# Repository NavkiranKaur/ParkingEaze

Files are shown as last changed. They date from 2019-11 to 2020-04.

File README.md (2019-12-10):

# ParkingEaze Project
## Build instructions
## Bipolar Stepper motor driven by Drv8825 driver on the raspberry pi broadcom platform
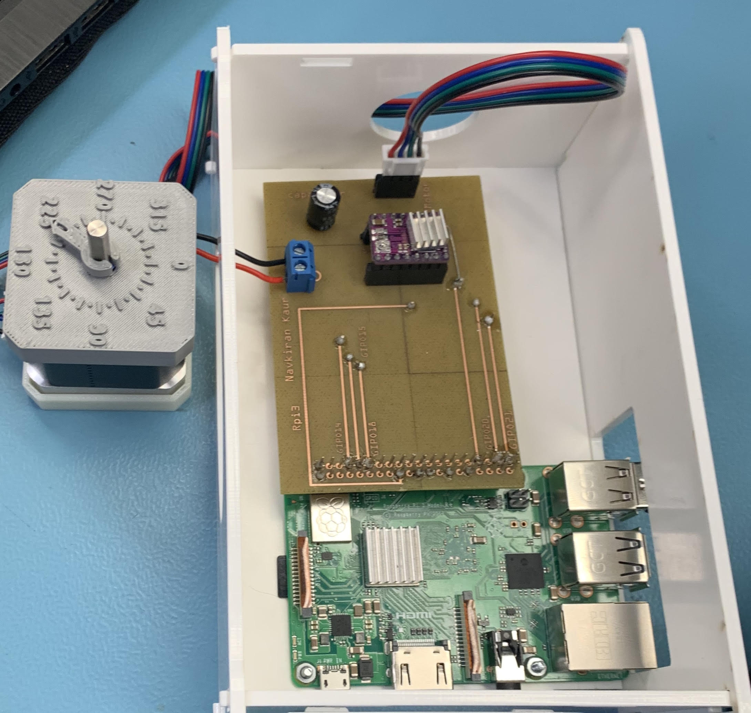
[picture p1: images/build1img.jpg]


## Purpose
The ParkingEaze Capstone Project : The stepper motor will be able to move the barriers in the car parking in order to allow the entrance and exit of the vehicle using the rotational movement controlled by the driver and raspberry pi Broadcom.
## Table of Contents
1. [Introduction](#introduction)
2. [System Diagram](#system-Diagram)
3. [Materials](#materials)
4. [Budget](#budget)
5. [Time Commitment](#time-Commitment)
6. [Setting up Raspberry Pi](#setting-Up-Raspberry-Pi)
7. [Mechanical Assembly](#mechanical-Assembly)
8. [PCB Soldering](#pcb-Soldering)
9. [PCB Power up](#pcb-power-up)
10. [Unit Testing](#unit-Testing)
11. [Enclosure](#enclosure)
12. [Production Testing](#production-Testing)

##  Introduction
In this project,bipolar stepper motor that is Nema 17 is driven by the DRV8825 driver on the raspberry pi development platform.Here are the build instructions that demonstrates how to control bi-polar stepper motors on a Raspberry Pi in Python using a DRV-8825 stepper motor driver.

## System Diagram 
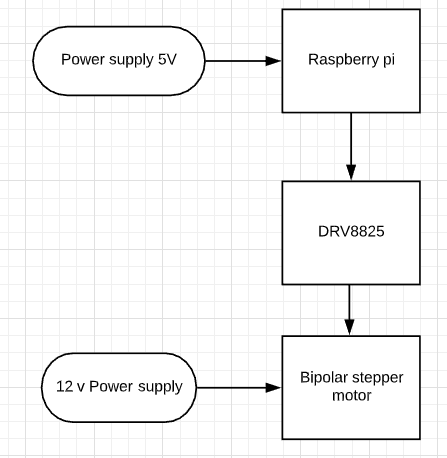
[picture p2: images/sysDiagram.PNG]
systemdiagram


## Materials
- Raspberry Pi 3B+ 
- [Hdmi cable](https://www.amazon.ca/gp/product/B07BN874RP/ref=ppx_yo_dt_b_asin_title_o02_s00?ie=UTF8&psc=1)
- [Bipolar steper motor Nema 17](https://www.amazon.ca/gp/product/B07C1MVTZC/ref=ppx_yo_dt_b_asin_title_o08_s00?ie=UTF8&psc=1)
- [Drv8825 driver](https://www.amazon.ca/gp/product/B07L2TKLPW/ref=ppx_yo_dt_b_asin_title_o08_s00?ie=UTF8&psc=1)
- [12 Voltage dc power supply portable adapt3r](https://www.amazon.ca/gp/product/B06X1BJRCS/ref=ppx_yo_dt_b_asin_title_o06_s00?ie=UTF8&psc=1)
- [Safety Glasses](https://www.amazon.ca/gp/product/B007YCMOCE/ref=ppx_yo_dt_b_asin_title_o05_s00?ie=UTF8&psc=1)
- power supply of the pi,mouse and keyboard
- 100 microFarad capacitor
- Breadboard and jumper wires (male and female)
- 40 pin male double row male to female header, 
- two 8 pins male to female headers and one 4 pin header ( all single row)
- Acrylic case for the enclosure 
- Get my Corel Draw file by clicking [here](https://github.com/NavkiranKaur/ParkingEaze/blob/master/mechanical/EnclosureFinal.cdr) for the enclosure
- 3d printed motor parts 
- Click [Here](https://github.com/NavkiranKaur/ParkingEaze/tree/master/mechanical/Nema%2017%20motor%203D%20printing%20files) to get my 3D printing files for the motor enclosure
-I suggest you to have them earlier so you could save your time instead of making them at the last end.

## Budget
- The main stuff and the materials required to build the project are listed below
The equipments that I have used from my parts kit are Jumper wires(both male and female),screw driver ,100 microFarad capacitor.I listed them here as in my budget my parts kit is mentioned,not the specific parts that I used.All the parts are bought from amazon except the parts that I already owned and the mouse,keyboard combo that is bought from Walmart.
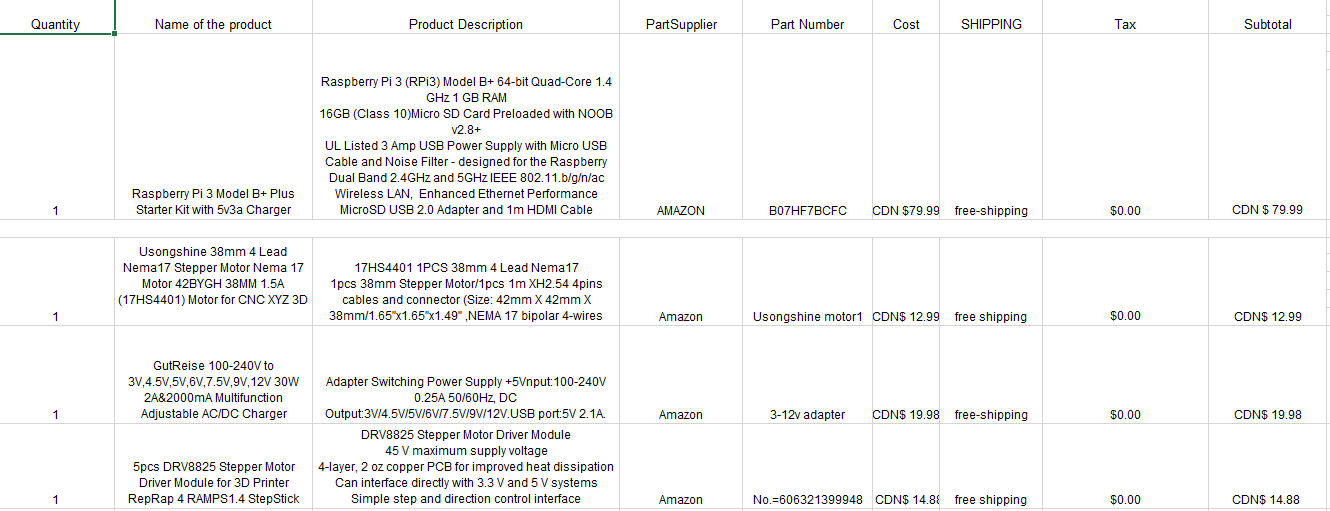
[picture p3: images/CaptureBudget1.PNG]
capture

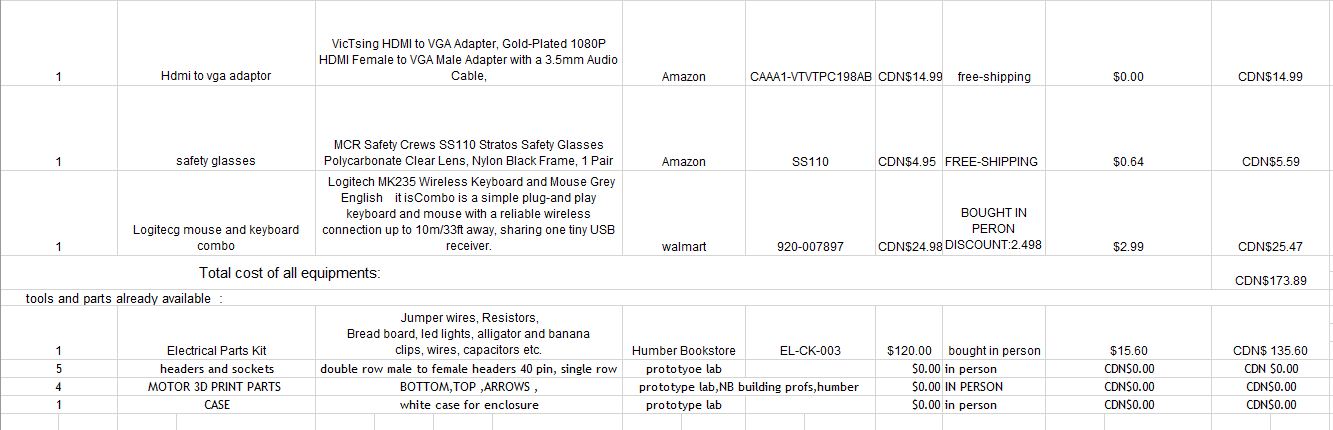
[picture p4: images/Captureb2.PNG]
capture


## Time commitment
- Overall project can be done in couple of days depends on the getting pcb made,alongwith making an enclosure for the equipments once they are built and connected.Also,depends upon the arrival of the materials for building hardware project.
In my case,I got delay in my breadboard due to not setting current voltage specifications on the driver,also made the pcb second time and also spent more time on the enclosure as it was 3D printing for the motor and my case was also big consisiting of pcb on the pi with the driver on it.So,if to be explained in more depth by knowing and being prepared what to do ,it can save much time.Breadboard can take 1 or 2 hours as to set all the voltages and making connections and based on that getting the pcb ready.Powering up take about 20 minutes and then getting the parts enclosed.

## Setting up raspberry pi
Connecting the raspberry with power supply,hdmi cable from raspberry pi to the hdmi to vga cable and that vga side to the monitor.Connecting the separate mouse and the keyboard with the pi.
Following the steps below:
1. Download [Raspbian](https://www.raspberrypi.org/downloads/) to be installed on your raspberry pi.
2. Use [SDCardFormatter](https://www.sdcard.org/downloads/formatter_4/) to format your SD card so for getting the pi to work
3. Inserting the SD card in raspberry pi and ensuring the connection all the above mentioned parts to be connected appropriately.
4. Switch on the power and finish the further setup including changing the settings.
5. Giving the commands on the terminal that require insallation like sudo updates etc,

## Mechanical Assembly
For the mechanical assembly,ensure connecting the pins and connections carefully.
Firstly the connections were made on the breadboard using the jumper wires from the driver ,raspberry pi ,stepper motor and the capacitor.I made the connections from driver to the raspberry pi ,motor and the capacitor and also used the power supply of the college. Breadboarding is just to make sure if the effectors and the components works as expected or their is a need to change some connections or if there is a damaged component.

## Wiring connections
-Raspberry pi pin 3v : DRV8825 SLEEP,DRV8825 RESET 
- Where connecting the sleep and reset together whereas connecting pi to the one of them
- Raspberry pi pin GND : DRV8825 GND1
- Raspberry pi pin GPIO21 : DRV8825 STEP
- Raspberry pi pin GPIO20 : DRV8825 DIRECTION
- Raspberry pi pin GPIO14 : DRV8825 MS1
- Raspberry pi pin GPIO15 : DRV8825 MS2
- Raspberry pi pin GPIO18 : DRV8825 MS3

ALSO IN DRV8825
-DRV8825 GROUND 1 TO BE CONNECTED WITH GROUND2 of DRV8825 itself
-In order to bind the motor wire pins with the drv8825
- Motor has two coil pairs Coil pair 1 ,coil pair 2
- Coil pair 1 includes A and C
- Coil pair 2 includes B and D
- MOTOR A WIRE PIN : DRV8825 OUT 2B
- MOTOR C WIRE  PIN: DRV8825 OUT 2A
- MOTOR B WIRE PIN : DRV8825  OUT 1A
- MOTOR D WIRE  PIN: DRV8825  OUT 1B

- MOTOR POWER SUPPLY ADAPTOR OF 12 V
- Capacitor (positive side) : DRV8825 VOLTAGE PIN : POWER SUPPLY POSITIVE (12V)
- Capacitor(negative side): DRV8825 GROUND: POWER SUPPLY GROUND

- Pin can be connected vice versa but make sure coil pair pins goes with the pair on the driver ,not interchanging if connecting a pair both pins to be connected to other driver pair itself. Don’t connect the pin in the pairs differently.

This [tutorial](https://www.rototron.info/raspberry-pi-stepper-motor-tutorial/) can also help you in depth with the required specifications.

--My breadboard design in the fritzing
capture
<!--![capture](https://raw.githubusercontent.com/NavkiranKaur/ParkingEaze/master/images/bread2.jpg)
![capture](https://raw.githubusercontent.com/NavkiranKaur/ParkingEaze/master/images/bread3.jpg) -->

- Also you need the code to run it,that i will be describing in the later steps below.

## PCB Soldering
Before starting the pcb soldering,make sure you watch this [video](youtube.com/watchv=BLfXXRfRIzY&list=PLQ32vZrF5U2lFOJTtZDytBWBYVLNp4RYz) and make sure to wear safety glasses.
The pcb is designed as followed by connections made and tested using the breadboard.
The pcb design is shown below designed in fritzing
capture
The pcb is made and then after it is soldered carefully
- Remember in my pcb design I put my drv8825 ground to ground connection on differnt side layer(yellow) than the soldering connecting pins (which are in orange).Make sure to keep it as same layer as other drv8825 connections.Hence ,you can see in my pcb ,i coonected an insulated red colour wire on same side where other drv8825 wires are connnected to pins.
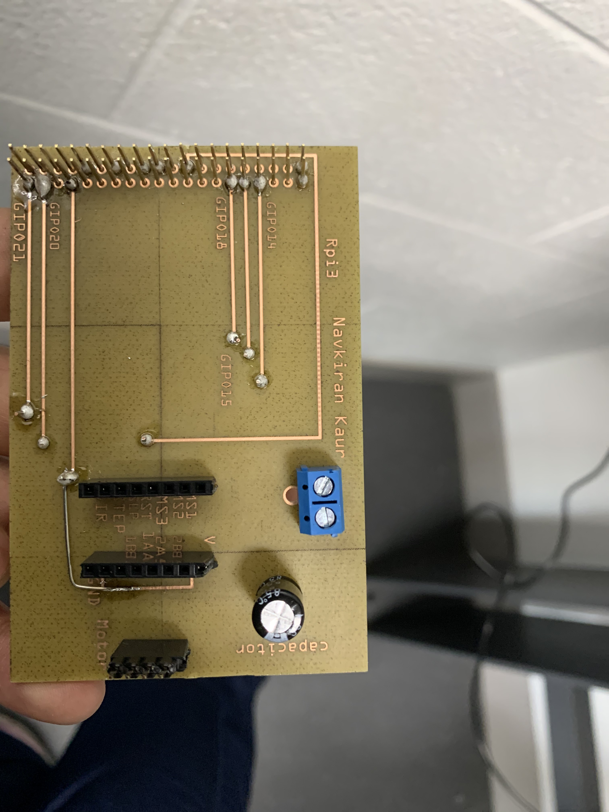
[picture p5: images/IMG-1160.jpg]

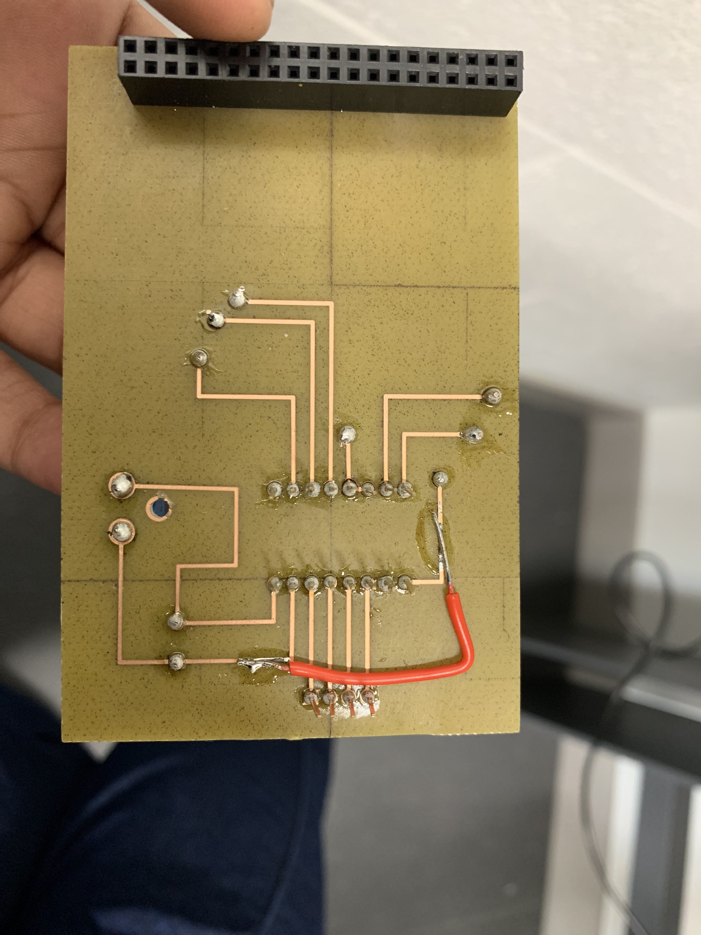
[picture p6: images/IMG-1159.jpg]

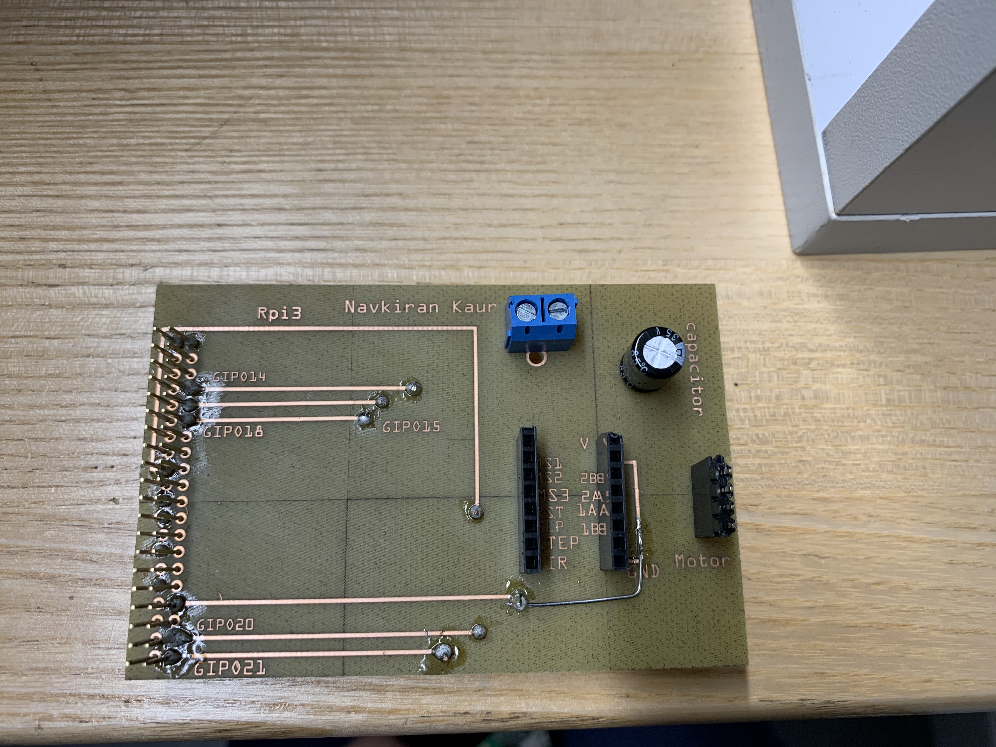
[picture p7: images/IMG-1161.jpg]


## PCB Power up
- Firstly make sure any of the pcb wire is not shorted.
capture

- pcb powering up 
capture
capture

The movement of my motor can be seen [here](https://github.com/NavkiranKaur/ParkingEaze/blob/master/images/IMG-0766.mov)

## Unit Testing
This is the code that i have used to run my motor in the python.
```
from time import sleep
import RPi.GPIO as GPIO

DIR = 20   # Direction GPIO Pin
STEP = 21  # Step GPIO Pin
CW = 1     # Clockwise Rotation
CCW = 0    # Counterclockwise Rotation
SPR = 100  # Steps per Revolution (360 / 7.5)

GPIO.setmode(GPIO.BCM)
GPIO.setup(DIR, GPIO.OUT)
GPIO.setup(STEP, GPIO.OUT)
GPIO.output(DIR, CW)

MODE = (14, 15, 18)   # Microstep Resolution GPIO Pins
GPIO.setup(MODE, GPIO.OUT)
RESOLUTION = {'Full': (0, 0, 0),
              'Half': (1, 0, 0),
              '1/4': (0, 1, 0),
              '1/8': (1, 1, 0),
              '1/16': (0, 0, 1),
              '1/32': (1, 0, 1)}
GPIO.output(MODE, RESOLUTION['1/8'])

step_count = SPR * 32
delay = .0208 / 32
#step_count = SPR
#delay = .0208
print("FORWARD")
for x in range(step_count):
    GPIO.output(STEP, GPIO.HIGH)
    sleep(delay)
    GPIO.output(STEP, GPIO.LOW)
    sleep(delay)
print("REVERSE")
sleep(.5)
GPIO.output(DIR, CCW)
for x in range(step_count):
    GPIO.output(STEP, GPIO.HIGH)
    sleep(delay)
    GPIO.output(STEP, GPIO.LOW)
    sleep(delay)
print("DONE")
GPIO.cleanup()
```

- Getting the outputs that enable rotation of the motor
capture
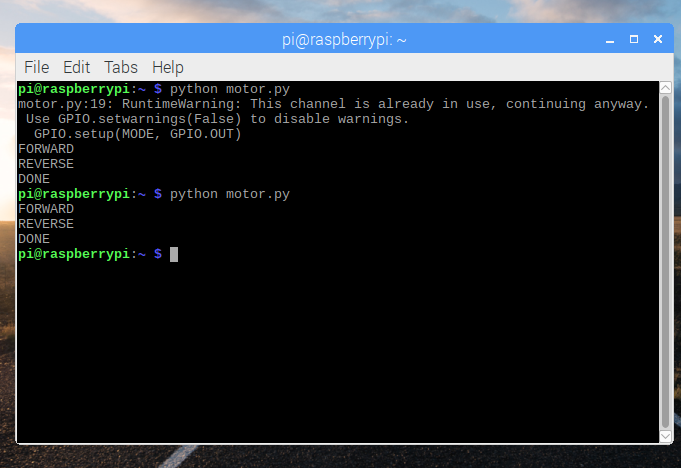
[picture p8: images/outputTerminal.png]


## Enclosure
- I got an acrylic white case enclosure that encloses my raspberry pi,driver drv8825 and the pcb 
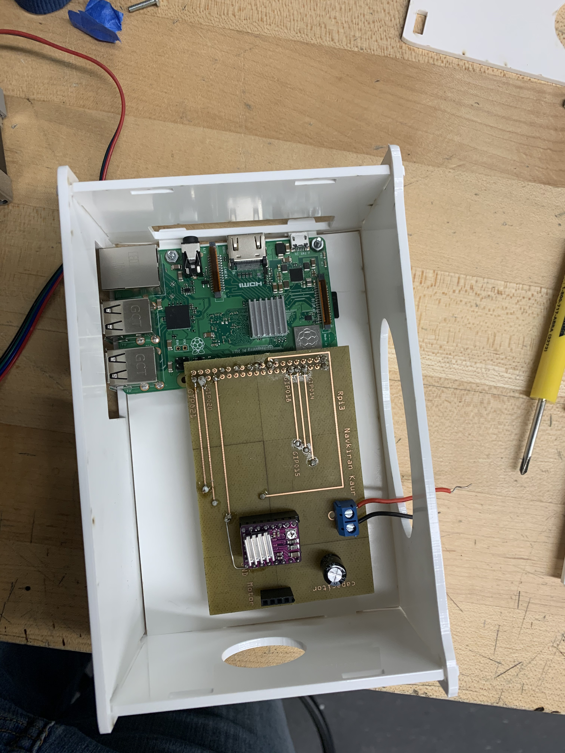
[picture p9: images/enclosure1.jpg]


- For my motor ,i got my parts as made with 3D printing.
- Click [Here](https://www.thingiverse.com/thing:3753538) to get the website for more information to design the motor 
- I got my 3D printed parts for motor from the humber college itself 

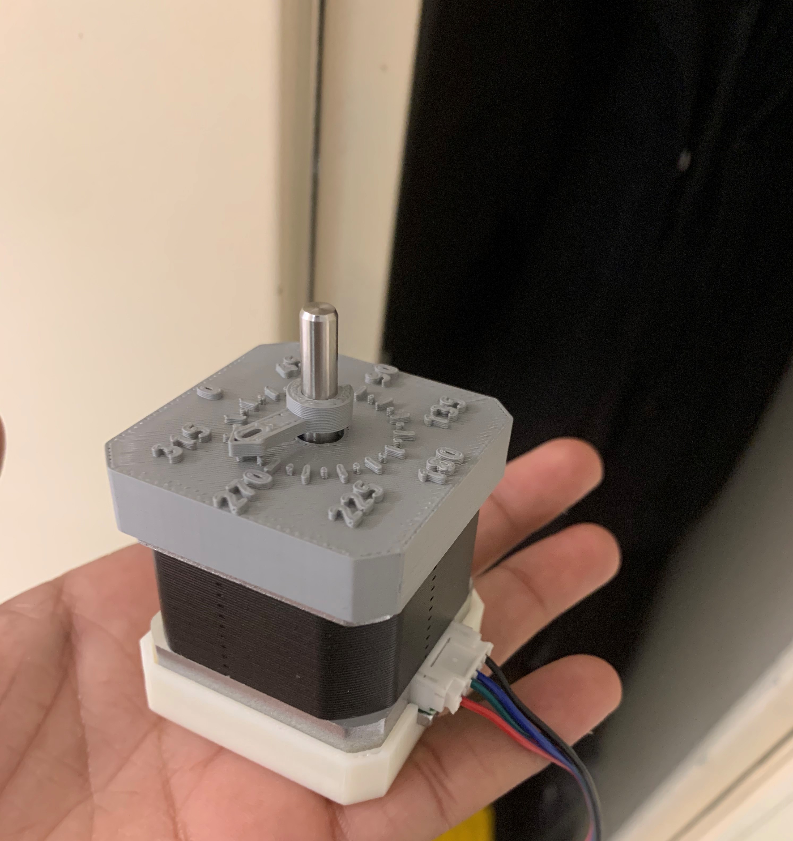
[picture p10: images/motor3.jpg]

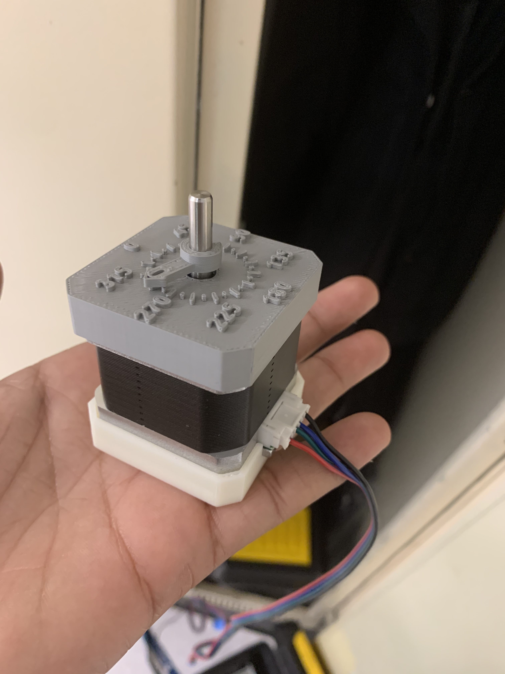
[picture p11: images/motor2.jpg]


## Production Testing
It is a crucial step to ensure that the parts work correctly and perform the required functions that are neccesary to executing the building hardware.In my project,the key thing to specify the voltage on the driver and limiting the current on it .Without doing it,the motor is not able to rotate which is the main requirement from the hardware production.
- Remember during the wires connection,make sure the voltage is not on,do not remove or plug in any wire while the power supply is plugged in.

- Hence,this is all about my project,I hope you get all the information in order to build this hardware project.

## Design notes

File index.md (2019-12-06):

<html>
  <head>
       <u> <h1> Project Blog: Parking IOT system scale model</h1> </u> <br> 
    <h2>Updates</h2>
    <p>
    <a href="https://github.com/NavkiranKaur/ParkingEaze/blob/master/documentation/PARKING%20EAZE_updated.pptx">Click to view Presentation</a> </p>
    <p> I updated my presentation as I corrected and update the price of safety glasses in the slide
    </p>
    <p>The updated budget of my project is here: 
         <a href="https://github.com/NavkiranKaur/ParkingEaze/blob/master/documentation/Budget%20updated%20final.xlsx">Click to view Budget</a>
     <h2>Posting the presentaion </h2>
    <p> My presentation link to the slides is 
      <a href="https://github.com/NavkiranKaur/ParkingEaze/blob/master/documentation/PARKING%20EAZE.pptx">here.</a>
      Previously,i was unable to load it as size was larger due to the video that i have included here but had to remove so the presentation can be uploaded.<p>
    <h2>Enclosure</h2>
     <p> My enclosure has been accomplished as it encloses raspberry pi,drv8825 driver and the pcb.For the motor ,i considered 3Dprinting.My corel draw file can be found 
       <a href="https://github.com/NavkiranKaur/ParkingEaze/blob/master/mechanical/EnclosureFinal.cdr">here.</a>
         <br>For the motor,design files for 3D printing can be found 
         <a href="https://github.com/NavkiranKaur/ParkingEaze/tree/master/mechanical/Nema%2017%20motor%203D%20printing%20files">here.</a>
      
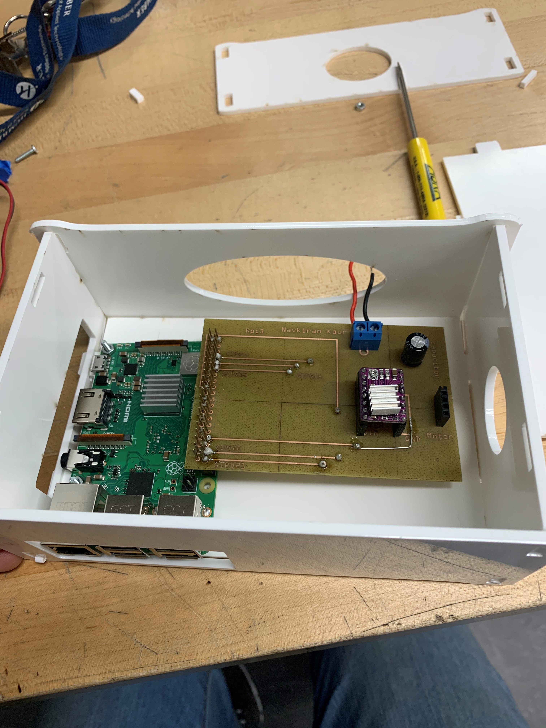
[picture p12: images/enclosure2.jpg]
      
      
       
    <h2>Nov 21 ,2019 </h2>
      <u> <h2> Progess report  </h2> </u> 
    <p> I was struggling with my motor working but it finally works as their some voltage and current specifications on the driver needs to be changed with the multimeter probes.Alongwith it ,the motor wires to the driver were connected in a wrong manner,so that implements the alterations on the pcb design.I soldered the new pcb with new changed connections of wire alongwith adding  power supply holes too as i am using a 12 v power supply for the motor.I am working for my enclosure case as this is the very next step after the powering up of the pcb. I had also ordered the hdmi to vga cable and bought a  mouse and a keyboard combo two weeks ago in order for running code on raspberry pi that also implies my changes in the financial status.b</p>
      <h2>Nov 14 ,2019 </h2>
    <p>The pcb is connected to the stepper motor,drv8825and the pi and the power supply from dc adaptor of 12 v is given and the motor is rotating ,forward ,reverse directions.The working pcb is demonstrated.
      <br>
       
       
      
       
      <br> the video of motor rotation can be seen through here
        <a href=" https://github.com/NavkiranKaur/ParkingEaze/blob/master/images/IMG-0766.mov">Click to view </a>
     <h2>Nov 13 ,2019 </h2>
    I acquired my new pcb and started working on it.The images are captured.
      
    
      
      .and updated new fritzing images are follows:
    
    
   
    <h2>Nov 12 ,2019 </h2>
    <p> In the prototype lab , i made the breadboard connections and raspberry pi broadcom and with the instructions and under guidance and help of professor Kelly gray , i made my motor works finally as with respect to the current and voltage specifications are to be considered.I used the dc power supply and the code works fine with motor movement.
      <br> I decided to design the pcb again.
     <br> the link to the site that is used to work out on my project can be found here
      <a href="https://www.rototron.info/raspberry-pi-stepper-motor-tutorial/">Click to view </a>
      <br> 
      the pictures taken can be found here
         
         
       
       
     <br> the movement of motor is also recorded.
      <br>video can be viewed by after clicking and going to this link below
      <br>  https://github.com/NavkiranKaur/ParkingEaze/blob/master/images/IMG-0682.mov
      <h2> Nov 7 , 2019 </h2> 
    <p> update: this is my old pcb that was demonstrated in class.<p>
    <p> The demonstration of the soldered pcb is presented in the class as the multimeter used to measure resistance by connection to power and ground of the raspberry pi and the output displays the overload that signifies the connection is open<p>
        
        
        
        
       <h2> October 29 , 2019 </h2> 
    <p> The breadboard is made so far with the stepper motor,jumoer wires,drv8825 driver and the raspberry pie </p>
    <br>
    <h3>Breadboard includes the connections of jumper </h3>
     
    <br> 
    <h3>
      The codes and the screen capture images of the outputs </h3>
      <br> 
      <br> 
      <br>
   <br>
    <h2> October 16 , 2019 </h2> 
    <p> The schematic ,breadboard and pcb fileas are created in fritzing and these are shown below</p>
    <p> Also, the fritzing files are sent as gerber files to the prototype lab for the pcb <p>
    <br>
    <h3> Schematic </h3>
     <br> 
  <h3>Pcb design </h3>
    <br>
    <h3>Breadboard </h3>
       <br>
     <h2> October 8 , 2019 </h2> 
    <p> Brought all the purchased parts in the class and showed the acquisations</p>
    <h2> October 1 , 2019 </h2> 
    <a href="https://github.com/NavkiranKaur/ParkingEaze/blob/master/documentation/Proof%20of%20purchase.pdf">proof of purchase</a>
   <b> <u> <p> Products purchase proof is posted on blog </p> </u> </b>
    <h2> September 24, 2019 </h2>
    <a href="https://github.com/NavkiranKaur/ParkingEaze/blob/master/documentation/Budgetproject.xlsx">Click to view Budget</a>
   <b> <u> <p> Budget of the parts is prepared after selection of the required tools</p> </u> </b>
    <p> Bioplar stepper motor <br> DRV8825 driver <br> Raspberry pi <br> Power supply Adaptor <br> 100 microfarad capacitor ,jumoer wires from the tools kit </p> 
     <h2> September 17, 2019 </h2>
        <a href="https://github.com/NavkiranKaur/ParkingEaze/blob/master/documentation/ProjectSchedule.mpp">Click to view Schedule</a>
   <b> <u> <p> Project Schedule  </p> </u> </b>
      <h2> September 10, 2019 </h2>
    <a href="https://github.com/NavkiranKaur/ParkingEaze/blob/master/documentation/proposal.xlsx">Click to view proposal</a>
   <b> <u> <p> Submission of Project Proposal  </p> </u> </b>
    <h2> September 3, 2019 </h2>
   <b> <u> <p> Selection of the project on Parking Iot scale Model  </p> 
  <p> Creation of the Repository </p> </u> </b>
  </head> 
    <body>
  </body>
  </html>

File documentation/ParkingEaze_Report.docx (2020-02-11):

ParkingEaze

Parking IOT system scale model

Navkiran Kaur

Saina Kapoor

Harleen Kaur Saini

Computer Engineering and Technology

Status

/1 Hardware present?

/1 Title Page

/1 Declaration of Joint Authorship

/1 Proposal (500 words)

/1 Executive Summary

# Declaration of Joint Authorship

We, Navkiran Kaur, Saina Kapoor and Harleen Kaur Saini confirm that this work submitted is the joint work of our group and is expressed in our own words. Any uses made within it of the works of any other author, in any form (ideas, equations, figures, texts, tables, programs), are properly acknowledged at the point of use. A list of the references used is included. The work breakdown is as follows: Each of us provided functioning, documented hardware for a sensor or effector. Navkiran Kaur provided the bipolar stepper motor that will be able to move the barriers in the car parking in order to allow the entrance and exit of the vehicle using the rotational movement controlled by the driver and raspberry pi Broadcom. Saina Kapoor provided the PCF8574 LCD with HC-SR04 ultrasonic distance sensor in order to measure the distance of the car and display it on the LCD screen on the raspberry pi. Harleen Kaur Saini provided Ek1245 infrared sensor on the raspberry pi will detect the presence of any vehicle parked in the parking spot. In the integration effort Saina Kapoor is the lead for further development of our mobile application, Navkiran Kaur is the lead for the Hardware, and Harleen Kaur Saini is the lead for connecting the two via the Database.

# Proposal

We have created a mobile application, worked with databases, completed a software engineering course, and prototyped a small embedded system with a custom PCB as well as an enclosure (3D printed/laser cut). Our Internet of Things (IoT) capstone project uses a distributed computing model of a smart phone application, a database accessible via the internet, an enterprise wireless (capable of storing certificates) connected embedded system prototype with a custom PCB as well as an enclosure (3D printed/laser cut), and are documented via this technical report targeting OACETT certification guidelines.

Intended project key component descriptions and part numbers
Development platform: Raspberry Pi 3B+
Sensor/Effector 1: PCF8574 LCD effector/ HC-SR04 ultrasonic sensor

PCF8574 LCD module is controlled by I2C bus to convert the parallel interface to a serial one. This needs only 2 wires SDA & SCL, apart from the power connections and ground. There is a blue model which adjusts the contrast of the LCD.

HC-SR04 ultrasonic sensor is a distance measuring transducer sensor which needs power supply of 5V DC and working current is 15mA. It has both transmitter and receiver modules and offers excellent non-contact range detection with high accuracy and stable readings

Part number: PCF8574 LCD module - IF-modulen_11747

Part number: HC-SR04 ultrasonic sensor- EL-SM-001

Sensor/Effector 2: EK1254 IR sensor

EK1254 infrared sensor is used in obstacle avoidance car, line count etc. It can be used for 3-5V DC power supply modules and detects the distance between 2 to 30cm and the output port OUT sensor module can be directly connected to the microcontroller IO port.

Part number: EK1254 infrared sensor- EK1254

Sensor/Effector 3: DRV8825 Bipolar Stepper motor

Bipolar stepper motor is the Nema 17 stepper motor that uses the full coil having two leads per phase that is four leads in total, having high torque, low noise, low self-inductance reactance. The motor is driven by DRV8825 driver with 45 V maximum supply voltage which has 4-layer, 2 oz copper PCB for improved heat dissipation which can interface directly with 3.3 V and 5 V systems.

Part Number: Stepper motor- Usongshine motor1, ASIN: B07C1MVTZC

Part Number: DRV8825- 606321399948, ASIN: B07L2TKLPW

We will continue to develop skills to configure operating systems, networks, and embedded systems using these key components to make our project work successfully. Daily parking, navigation problems and time constraint were taken into consideration to give a prominent solution so by the end of this project a better parking facility will be delivered to the customers using our simple application. Sensors will collect the data and will show in the application about the count of spaces available. Within one click, user will get booked location in the app and will park the car at the destination without any delay. A major change in the navigation is that the directions will be available as soon as the driver enters the parking lot in order to direct to the correct parking spot. Our hardware and software components offer a better usability and testability that will also store user’s information in the database along with time slots, credit card information, login credentials, license plate number, etc. This will prevent the traffic congestions as everything will be done already in the app.

Our project description/specifications will be reviewed by the Department of Public Safety, Humber College, ideally an employer in a position to potentially hire once we graduate. They will also ideally attend the ICT Capstone Expo to see the outcome and be eligible to apply for NSERC funded extension projects. This typically means that they are from a Canadian company that has been revenue generating for a minimum of two years and have a minimum of two full time employees.

The small physical prototypes that we build are to be small and safe enough to be brought to class every week as well as be worked on at home. In alignment with the space below the tray in the Humber North Campus Electronics Parts kit the overall project maximum dimensions are 12 13/16" x 6" x 2 7/8" = 32.5cm x 15.25cm x 7.25cm.

Keeping safety and Z462 in mind, the highest AC voltage that will be used is 16Vrms from a wall adapter from which +/- 15V or as high as 45 VDC can be obtained. Maximum power consumption will not exceed 20 Watts. We are working with prototypes and that prototypes are not to be left powered unattended despite the connectivity that we develop.

# Executive Summary

Parking is a worldwide problem, especially when people are unaware about spaces, costs and policies that results in waste of time, crowding and frustration. Our project aims to solve these problems by using such sensors and effectors which in coordination with our mobile application makes it easier for our users to park and pay in a fast and efficient manner. With the help of our technical skills and professor’s guidance we used the features and key points of different sensors and effectors such as infrared sensor, ultrasonic sensor, Bipolar stepper motor, LCD module and customizable development of mobile application in order to deliver a trustworthy finished product under a low-cost budget.

# List of Figures

# 1.0 Introduction

Traffic flow, distribution, and accessibility of parking space, in these days, have been a major concern to every person in daily routine which makes it an important issue. There is a lot of consummation of time and resources for drivers who spend their precious time driving along the streets in search of parking space and then also going through the long process to pay the parking fees. To solve this necessity of vehicle parking, we introduce a parking project called ParkingEaze. The ParkingEaze Project enables customers/drivers to online reserve a parking space using the mobile application. The purpose of this project is to provide the user the convenience to park their vehicle as per their requirement using the app. It allows the user to view the parking status and its location in the android device application. This project is developed to tackle the traffic congestion, collision, and delays faced by the people in their daily life which results in a lot of headaches, frustration, and wastage of time. The project includes the software and hardware integration that will determine the execution of our project. The spots for booking that we include and consider for reservation belongs to the Humber college. The hardware part of the project would be having raspberry pi as a development platform. Along with that infrared sensor, ultrasonic sensor, bipolar stepper motor, LCD module contribute as a major portion for project development. The bipolar stepper motor will allow the entrance and exit of the vehicle while the LCD will show the booked parking spots. The infrared sensor will detect the presence of the vehicle in the parking area also determines the obstacles. Coming to the software, an android app called ParkingEaze is designed on the android studio which users can log in to reserve the vacant slots online. This android application called ParkingEaze is created for the user to reserve an empty parking spot from the locations mentioned above. The mobile application is constructed through java language which can run on android devices using the android studio as a platform for its development. The app provides rich user experience and eases to utilize the time. Also, the issues of losing the paper ticket, waiting in lines to park are solved while using this system. After booking the parking spot in the app, the user will select the date and duration of the time during which the vehicle needs to parked and then an online payment method is performed. Afterward, the user will be allotted a parking spot where the vehicle can be parked. The project is scheduled to be accomplished in a certain time in which the mobile application and the individual hardware projects are developed in the first four months. The hardware and software integrations are performed in the last four months. Therefore, the project aims at solving a real-world problem by designing an android application system that will enable the customers to make a reservation of available parking space. The project mainly focusing on assisting the users and helping them to balance their working life easier by providing them a solution to the problem that has been faced by them daily in their lifestyle.

## 1.1 Scope and Requirements

In this project basically, we are going to combine our hardware and software courses that we have done in the previous semester. It is an Internet of Things (IoT) capstone project that uses a distributed computing model of a smartphone application, a database accessible via the internet, enterprise wireless (capable of storing certificates) connected embedded system prototype with a custom PCB as well as an enclosure (3D printed/laser cut), and is documented via an OACETT certification acceptable technical report. Also, there are some limits of the project like through our the app we will be able to book the parking spots of only the Humber college parking and what will not be done (CSA testing) in this project: we are not going to add any real-time card transactions, we were thinking to add license plate detector but that will not fit in our budget, so we are thinking to drop the idea.

Development platform specifications:

- We are using Raspberry pi 3(Rpi3) Model B+ having 64 bit quad-core 1.4 GHz,1 GB RAM.

Hardware specifications:

We are using different sensors in our project:

- Infrared sensor – to detect the presence of any vehicle parked in the parking spot.
- Ultrasonic distance sensor - to measure the distance of the car.
- LCD – to display it on the LCD screen on the raspberry pi.
- Bipolar stepper motor - to move the barriers to car parking.

the Android device requirements:

- Our app will be able to run on the android devices whose minimum API will be 23 i.e. marshmallow.

database specifications/protocols:

- We are going to use firebase, where we can store, extract and add the data.

Report

/1 Hardware present?

/1 Introduction (500 words)

/1 Scope and Requirements

/1 Background (500 words)

/1 References

# 2.0 Background

We would like to thank the Department of Public Safety and James Irvine, manager at Transportation and parking services, Humber College for supporting this project. We chose this project to solve the day to day problems related with parking, so for the smart solutions we researched about various sensors and effectors which can be taken into consideration to deliver a finished and efficient project called Smart Parking. We chose different sensors and effectors such as EK1254 IR sensor, an infrared sensor which sense the cars at the parking spot and shows if the parking spot is available or occupied (Ms.S.Srikurinji, 2016), the movement of Bipolar stepper motor,Nema 17, allows the vehicle to enter and exit the parking lot (The journal of design and technology, 2000).The bipolar stepper motor is driven by DRV8825 driver that will be capable of driving the motor .Lastly the HC-SR04 ultrasonic sensor that will the sense the object combined with the LCD module displays the distance of the cars to the parking spaces and the user is able to see what is displayed (GauravKumarMaurya, 2016). The idea of the application of smart parking is to provide ease to the customers within one click, user will get booked location in the app and will park the car at the destination without any delay. Our hardware components will collect the data and will be displayed in our application with certain features like the updating the parking lots and the location will take only few seconds (Kahonge, 2013).The development platform is the raspberry pi Broadcom that will be used to develop the parking project interacting with the sensors and effectors which are stated in the project. The project is developed on the basis of the requirements to fulfill the project needs for resolving the problem faced in the real world. The ParkingEaze application asks the user to register first and then login and all the data is added to the database. The information of the customer such as contacts, name, password etc. are the part of the database as it will be stored them as we are using the firebase for the project. Our project development will help us gain necessary skills in order to gain more knowledge and experience through exploration of ideas used in the hardware and software. The project explores the wide picture of the innovative and creative ability of integrating the components which will led to a successful accomplishment that will benefit the society.

# 3.0 Methodology

The project is called parkingEaze and here the required resources are mentioned below

## 3.1 Required Resources

The components that comprise the hardware project are bipolar stepper motor driven by drv8825 ,EK1254 infrared sensor and the lcd module with ultrasonic sensor

Report

/1 Parts/components/materials (500 words)

/1 PCB, case (500 words)

/1 Tools, facilities (500 words)

/1 Shipping, duty, taxes (250 words)

/1 Working time versus lead time (250 words)

### 3.1.1 Parts, Components, Materials

We are using Raspberry pi 3(Rpi3) Model B+ having 64 bit quad-core 1.4 GHz,1 GB RAM as our Broadcom.

Sensors or effector that we are using are:

Sensor/Effector 1: Gikfun IR Infrared Sensor EK1254

The output port OUT sensor module can be directly connected to the microcontroller IO port, you can directly drive a 5V relay; The module detects the distance 2 -30cm, detection angle 35 °, the distance can detect potential is adjusted Can be used for 3-5V DC power supply modules. When the power is turned on, the red power indicator light. This sensor will sense if the parking spot is available or not. This sensor will send the information to the LCD to display which parking lot is available. This is our one of the effectors that we will discuss in upcoming paragraphs

Sensor/Effector 2: Bipolar stepper motor driven by DRV8825 driver on the raspberry pi Broadcom

Bipolar stepper motor: It is the Nema 17 stepper motor that uses the full coil having two leads per phase that is four leads in total, having high torque, low noise, low self-inductance reactance.

The DRV8825 stepper motor driver has output drive capacity of up to 45V and lets you control one bipolar stepper motor at up to 2.2A output current per coil. This driver carrier is a breakout board for DRV8825 micro stepping bipolar stepper motor driver.

This sensor will be used at the entrance and exit of the parking area to raise up or down the boom barrier.

Sensor/Effector 3: pcf8574 LCD module: LCD module yellow-green screen PCF8574 IIC/I2C 1602 LCD. the dedicated IIC bus control, it only takes two IO. Adjustable contrast and backlight controllable Yellow and green screen.

This sensor will display the information of parking spots as if parking area is full or which parking spot is empty.

HC-SR04 ultrasonic sensor: Ultrasonic hc-sr04 distance measuring transducer sensor. HC-SR04 consists of ultrasonic transmitter, receiver, and control circuit. When trigged it sends out a series of 40KHz ultrasonic pulses and receives echo from an object having 5V DC, current less than 2Ma.

This sensor will sense the vehicle if it is coming nearby and will be connected with the bipolar stepper motor that will raise up the boom barrier when the vehicle is at certain distance.

Headers: Different headers are used that will be connected on the PCB so that our sensors can be easily connected or removed from the PCB board.

Resistors: We have used the resistors so that our sensors or effector does not get damage by high voltage. They are directly connected on the PCB through soldering.

Jumper Wires: They are used to connect the different parts of the bipolar stepper motor our stepper which can’t be directly connected with board.

Acrylic sheets: We need acrylic sheet for the enclosure. Although we’ll get sheets from the next door that is the prototype lab, but still this will be one of the requirements.

### 3.1.2 Manufacturing

## 3.1.2.1 PCB

To display a working module, we first designed the breadboard design so that it can be implemented on the printed circuit board in order to deliver finish working project. We used Fritzing software to draft the pcb which had multiple options to check if the connections were correct and exported with the help of Gerber files and it was made in the prototype lab. Starting with Saina’s project it consists of 1 HC-SR04 sensor which is connected with the LCD module and two resistors to display the distance of the car, to design the pcb it took multiple attempts to plan the correct board. In the very first attempt pcb was in the opposite direction of the raspberry pi which again led to second attempt in which Via points were not in correct order so the sensor was responding late, third attempt was to basically position the LCD in the horizontal manner which led to the fourth and the final attempt for the pcb which had all the requirements such as small and all the correct connections. Navkiran’s project includes bipolar stepper motor, capacitor, driver and power supply. It took hardly two attempts to design the pcb, in the first try the parts were disorganised and the pcb was huge which was taken forward to the second attempt, a mistake was made because of so many wires one wire was missed so it was soldered manually and the possibility of short was taken care of. Harleen’s project consist of an EK1254 infrared sensor which had a very simple connection with raspberry pi, this also took 2 attempts in order to fix the via points and to make the pcb smaller. Hence, the three printed circuit boards were made in the hardware production technology and these hardware will be integrated in to single project in this semester.

# 3.1.2.2 Case

To design the enclosure case, we used Corel draw software which was again printed in the prototype lab using the laser cut technique. Saina’s raspberry pi case was taken from one of the projects mentioned in the thingiverse website. All the sides except the top was made from white acrylic sheet and the top was made from clear acrylic sheet in order to see the readings on the LCD. Also, a notch was made for the sensor to take the readings. Harleen’s enclosure was also derived from thingiverse website and it was made from clear acrylic sheet however, a slit was made in the sidewise direction to make room for the sensor to sense the object. Lastly, Navkiran’s case fitted all the elements accurately but the bipolar stepper motor was connected through the jumper wires and it was placed outside the box because the motor was placed in the 3D printed case which was again inspired from one of the projects available at the thingiverse website.Therefore, for the enclosure, we have considered both laser cut printing and 3D printing which are learning resources gained from the hardware production course.

### 3.1.3 Tools and Facilities

The individual hardware projects which are involved in this project are accomplished using various tools and facilities. These privileges mainly include the facilities provided by Humber College itself. The prototype lab plays a vital role in the completion of our hardware projects. The prototype lab prepares a printed circuit board for students after getting the Gerber files from them. The prototype lab provides facility of the headers and sockets, soldering the pcb, jumper wires, wire cutters which are the required resources in our project. Moreover, the prototype also delivers the service of laser cutting and 3D printing. This is helpful at the time of the enclosure as the components are securely attached in the acrylic case enclosure. The prototyping lab staff were also very helpful in giving the instructions and guidance regarding the queries. They would also assist the students in terms of solving the issues related to hardware. Also, Humber faculty also helped in 3D printing of the bipolar stepper motor used in our project. The parts crib plays an important part in giving access to students with the essential tools needed for the practise and students understand and get to know about their functions in particular. The labs contain the soldering devices, multimeters, power supplies, oscilloscopes, and function generators etc. which are easily accessible to us while working on our hardware projects. These facilities contributed a lot in the execution of our projects and they will be helpful furthermore in the integration too. Without these facilities in college, it would have been very hard to work on the project from outside which would be very time consuming and costly. In addition to it, the soldering has been done in a safe environment as we are always asked to wear our safety glasses and proper and necessary equipment such as vacuum are available at the soldering spots. There is the Idea Lab in the college designed to support digital literacies at Humber College. The Idea Lab has three components: studio spaces, workshops, and online resources. They provide the facility of 3D printing and also guide us regarding it through conducting a workshop in the last semester. Humber libraries have been helpful in regard with access to the reading resources and also how to make references in the documentation. Coming to the tools, we have used fritzing for designing the printed circuit board and also making the schematic and breadboard connections through it. The CorelDraw application helps to create a .cdr file that is required to build the acrylic case. In the software application, we have used the android studio in order to design the mobile device application for the project. The android studio comprised of all the significant features that are capable of building the application for the users. Therefore, with the help of these tools and facilities, the hardware production technology projects and the android application has been accomplished. Hence, these resources perform a major role in the production of hardware and the software.

### 3.1.4 Shipping, duty, taxes

Before planning for the project, we worked on our individual budget and ordered the parts required from various sources and mentioned the taxes, duty and shipping cost in our final budget. Saina’s parts costed CAD $89.71 and tax of CAD $15.2 which made a total of CAD $104.91 all these items were bought from Amazon however; the shipping cost was free because of the subscribed member of the prime in Amazon. In Harleen’s project, apart from the sensor additional things were bought such as keyboard and HDMI to VGA converter which made a total of CAD $121.95 without any additional charge such as shipping, taxes etc. because of the prime membership with Amazon. Navkiran’s total cost amounted to CAD $173.89 of which the taxes were $3.63 and the shipping was all free as the components are ordered from amazon which also has the amazon prime facility for students. Some of the products are also bought in person from the store such as mouse and keyboards as they also contributed towards taxes.

### 3.1.5 Time expenditure

1. The working time has been different than the lead time which contributes to the whole time consumed by the project. The printed circuit board has taken around few hours to create design on the fritzing. Afterwards the time for pcb board to be made took around 1 and half day and then working on pcb such as soldering take half hour. For the ordered parts such as ordering on amazon take maximum 2 days as the amazon prime service was offered and available for the students. So, it took less time for delivering the products. However, product such as LCD module was delivered almost after 15 days as it took longer because it was shipped from another country. The schedule was prepared on the basis of the Gantt chart and the deadlines and due dates are considerably taken into effect with respect to time period. Although, the lead time mattered in the project yet the working time was appropriately adjusted and compensated according to the increased lead time. The lead time for the 3D printed motor was around a week which was more than the working time. The working time for the motor 3D printing only constituted for gathering 3D printing files and sending them for the creation. For the laser cutting, it took more time to create design in CorelDraw than actually having it laser cut that amounts to 2 or 3 days. The laser cut printing only took 15 minutes. For the software application, the working was more consuming basically while ensuring the connectivity to the database. Therefore, the time expenditure comes out as a vital factor and a determent of the outcomes for the hardware production and the software application.

## 3.2 Development Platform

### 3.2.1 Mobile Application

As a part of capstone project, we choose the parking problem as our project to solve the real-world problem. In the software project we develop an android application called ParkingEaze to provide the users with a facility to book a parking spot using this android application in order to tackle the traffic issues and delays in the working world. The android mobile application is developed on the android studio with the features that are contained within the android studio and implemented considering the requirements.

Test cases and plans implemented while developing the application

- Various test cases are implemented which includes all the validation for the email field and the password field such as in the register area. The test cases are passes that consists of the specifications.
- Password containing at least one number, an uppercase letter, a lowercase letter, the special character and the fields could not be empty.
- A splash screen is displayed when the user clicks on home icon of the app for a duration of 3 seconds.
- A dialog box appears if user click on soft back key, asking for either to exit or stay in the app.
- Around 11 test cases are implemented and tested in the android project
- There is a run time permission that asks the user to give the location access to the mobile application through displaying a dialog box when the application is started in the beginning.

We set some requirements for our android application which are further divided into functional and non-functional requirements

Functional requirements

- Mobile Application for end users requirements so they will be capable of using it
- Register for the parking and input personal and vehicle details.
- Finding a parking area from the list of areas
- View the details of a selected parking area.
- Reserve an available parking lot and specifying duration of reservation.
- For example, getting a confirmation once a slot is booked.

Non-functional requirements

- Availability: Independent platform so that it can be accessible and store app data
- Ability of server to handle simultaneous requests from different users.
- Confidentiality for user data using database encryption
- High availability and high accuracy in the locations finding
- Performance as to be started within a click
- Reliability for acknowledging the customer for any important action
- Ability to render its layout to different screen sizes

Mock-up discussion before developing the real application

- Mock-up discussion is based on the working sample for reviewing format and layout of the whole project.
- Used for experimental and instructional purpose

The mobile application is developed using the features such as runt time permission, location services, navigation drawer layout, java language, minimum api 23 which is marshmallow have been connecting it firebase but accomplishments to be made in this semester.The connection has been tried using the firebase but we are unable to connect it as we are getting the errors. We have researched regarding this issue but the connection to the firebase cannot be established despite the fact that we have tried a lot of attempts. We have consulted the software project professor in order to get further help regarding connectivity to database so the problem for this issue can be resolved.

Splash screen

When the user clicks on the homescreen of the application, the splash screen will appear for the duration of 3 seconds followed by a login screen that will ask user to login.

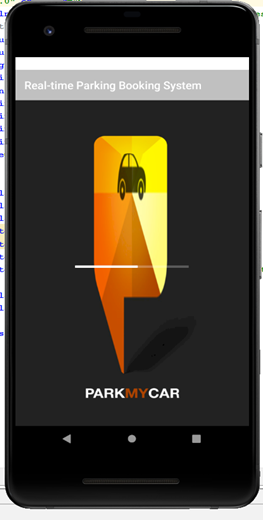
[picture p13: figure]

Figure 1: Splash screen view of the android application

Login Activity

Then comes the login screen where the user will have ability to enter the username and the password in order to login the application and it also has the register option which on the click will ask the user for registration if the user is not registered yet.

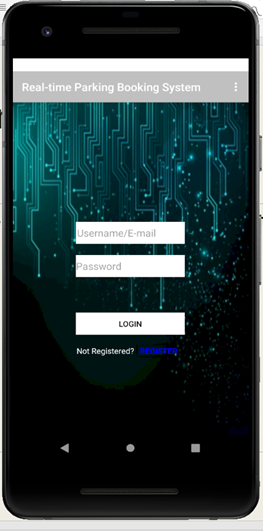
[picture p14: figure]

Figure 2 login screen view of the android application

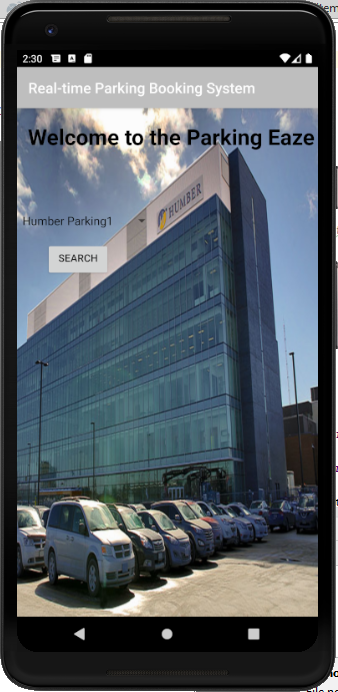
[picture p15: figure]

Figure 3 ;user asked to choose the parking location

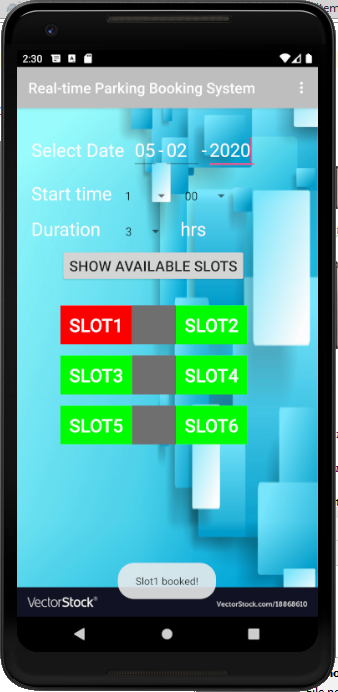
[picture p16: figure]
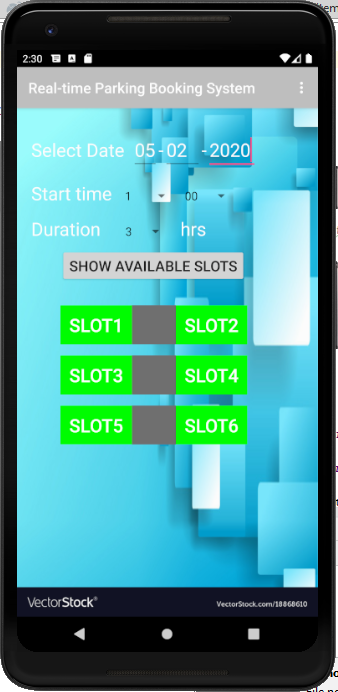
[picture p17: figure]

Data visualization activity

Figure 5 the user booked the parking slot which turns red

Figure 4the parking slots are shown which are empty

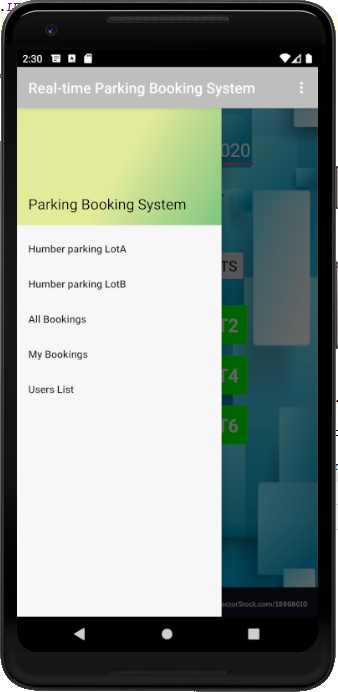
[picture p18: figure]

Figure 5 the navigation drawer layout has been implemented

Action Control Activity

After the user is logged in the mobile application, the location for the parking the vehicle are to be chosen from three options which are Humber Parking1, Humber Parking2 and Humber Parking3(Figure 3). The dialog box is displayed which shows these choices to user When the user clicks on one of the options then a new screen appears which asks the user to choose an empty parking spot(Figure4). The slot turns green to red (Figure5)after the user booked it and therefore the spot to park the vehicle has been booked by the customer through the android application.

Status

/1 Hardware present?

/1 Memo by student A + How did you make your Mobile Application? (500 words)

/1 Login activity

/1 Data visualization activity

/1 Action control activity

### 3.2.2 Image/firmware

This documentation depicts the structure of the code and connectivity to the raspberry pi. In the Navkiran's project, bipolar stepper motor that is Nema 17 is driven by the DRV8825 driver on the raspberry pi development platform. The Raspberry Pi is used to control bipolar stepper motors on a Raspberry Pi in Python using a DRV-8825 stepper motor driver. Saina’s project is to measure the distance of the car and display it on the LCD screen. The LCD screen will display the available parking spots and will give indication and direction to the customer and the HC-SR04 the ultrasonic sensor is also used with the LCD module. Harleen’s project is to reduce parking problems using the Ek1254 sensor. Ek1245 infrared sensor will detect if there is any car parked in the parking spot. These three-hardware production projects are developed on the raspberry model 3B+. The raspberry has been set up using connecting the raspberry with power supply, HDMI cable from raspberry pi to the HDMI to VGA cable and that VGA side to the monitor. Connecting the separate mouse and the keyboard with the pi. Following the steps below:

  - Download Raspbian to be installed on your raspberry pi.
  - Use SDCardFormatter to format your SD card so for getting the pi to work
  - Inserting the SD card in raspberry pi and ensuring the connection all the above-mentioned parts to be connected appropriately.
  - We downloaded the Raspbian image file that we download onto an SD card which in turn can be used to boot your Raspberry Pi and Via APC into the Raspbian operating system. Using a Raspbian image is the easiest way for a new user to get started with Raspbian.
  - Switch on the power and finish the further setup including changing the settings.
  - Giving the commands on the terminal that require installation like sudo updates etc.

These steps were followed in the last semester for setting the raspberry pi to the hardware.

Connection of VNC viewer to the raspberry pi

Cloud connections are convenient and encrypted end-to-end, and highly recommended for connections over the Internet. There’s no firewall or router reconfiguration and you don’t need to know the IP address of your Raspberry Pi or provide a static one that is why we used VNC viewer. For the authentication, to VNC viewer we needed to complete either a direct or cloud connection to VNC Server. After that, we entered the user name and password to log on to the user account on the Raspberry Pi. This is how our firmware got connected with the VNC viewer. This enables the wireless connectivity and the internet availability on raspberry pi should be similar to that of VNC viewers and that will ensure the connectivity. We are using raspberry pi and bipolar stepper motor which need the power supply as separate in order to operate as we need power cables for them. The foremost and major problem that we have faced is connecting the pi to the VNC viewer with the secure Wi-Fi network and still, there is the process of troubleshooting going on with the connection. The code used for the working of the hardware projects used in the last semester is written using the python language. The separate codes used for our individual projects are posted on the GitHub and we have provided the link below to access the software code.

https://github.com/NavkiranKaur/ParkingEaze/tree/master/firmware

Status

/1 Hardware present?

/1 Memo by student B + How did you make your Image/firmware? (500 words)

/1 Code can be run via serial or remote desktop

/1 Wireless connectivity

/1 Sensor/effector code on the repository

### 3.2.3 Breadboard/Independent PCBs

Status

/1 Hardware present?

/1 Memo by student C + How did you make your hardware? (500 words)

/1 Sensor/effector 1 functional

/1 Sensor/effector 2 functional

/1 Sensor/effector 3 functional

The initial schematic design, Figure 2, based on datasheets (Bosch Sensortec, 2019) led to a breadboard layout Figure 3 that was realized Figure 4.

How did you build your Prototype: Breadboard?

Then a PCB was designed, Figure 5, and populated (Figure 6). Bill of Materials, Case, Time commitment. Testing. Progress.

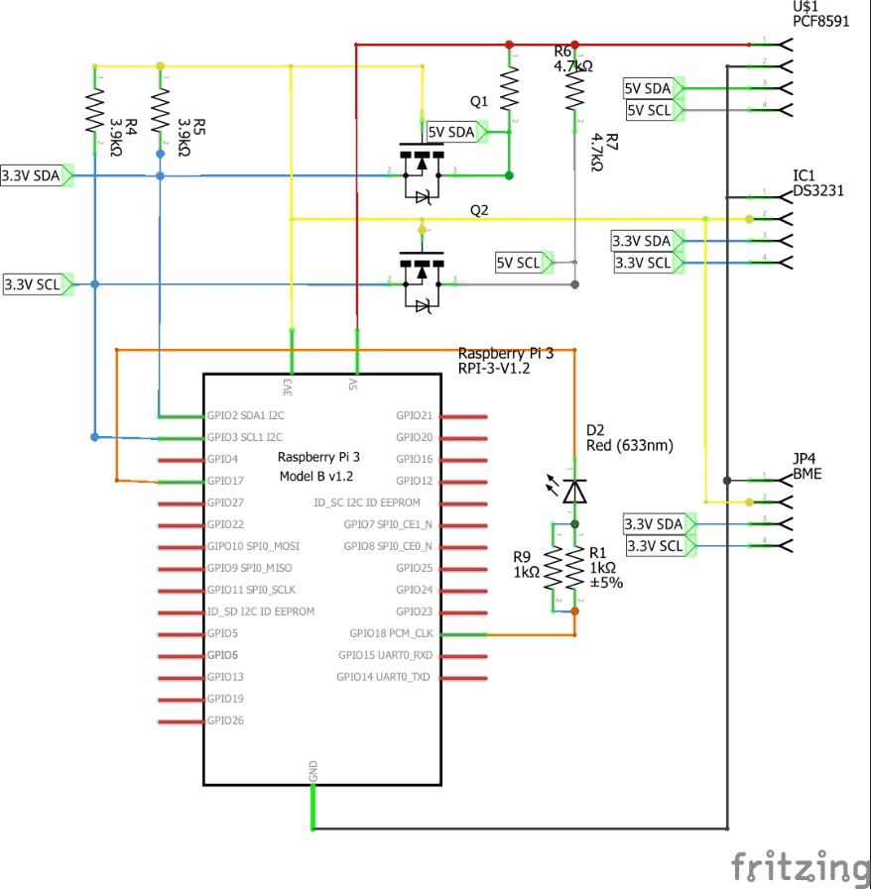
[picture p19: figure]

Figure 2. Initial schematic. This work is a derivative of "http://fritzing.org/parts/" by Fritzing, used under CC:BY-SA 3.0.

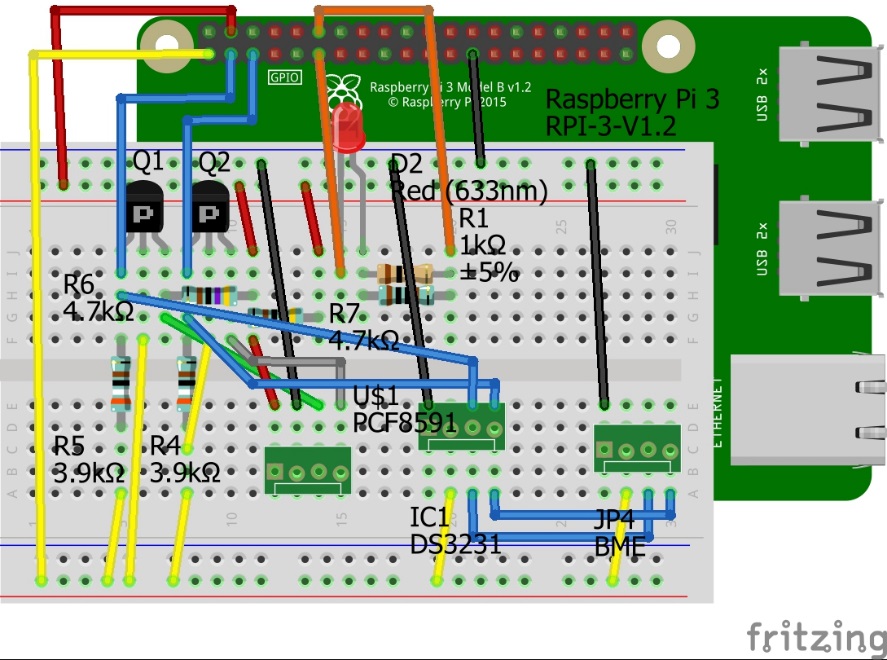
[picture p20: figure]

Figure 3. This work is a derivative of "http://fritzing.org/parts/" by Fritzing, used under CC:BY-SA 3.0.

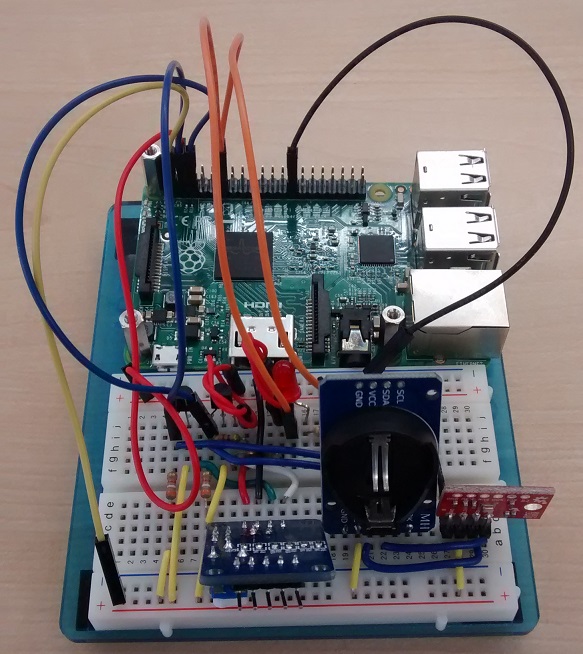
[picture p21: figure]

Figure 4. Breadboard prototype.

### 3.2.4 Printed Circuit Board

Demo

/1 Hardware present?

/1 PCB Complete and correct

/1 PCB Soldered wire visible but trim, no holes or vacancies

/1 PCB Tested with multimeter

/1 PCB Powered up

How did you build your Prototype: PCB?

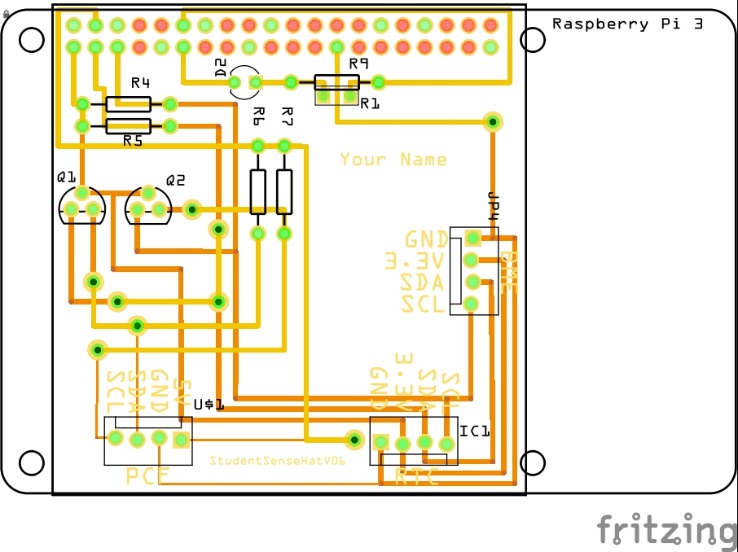
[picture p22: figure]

Figure 5. PCB design This work is a derivative of "http://fritzing.org/parts/" by Fritzing, used under CC:BY-SA 3.0.

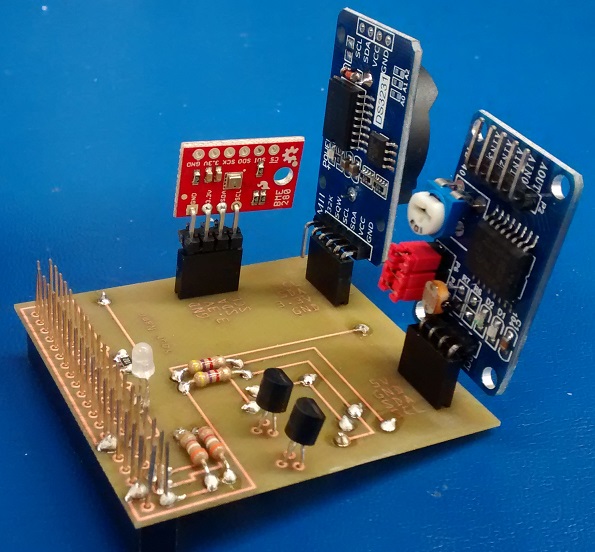
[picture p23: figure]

Figure 6. Humber Sense Hat Prototype PCB.

### 3.2.5 Enclosure

Demo

/1 Hardware present?

/1 Case encloses development platform and custom PCB.

/1 Appropriate parts securely attached.

/1 Appropriate parts accessible.

/1 Design file in repository, photo in report.

How did you build your Prototype: Case?

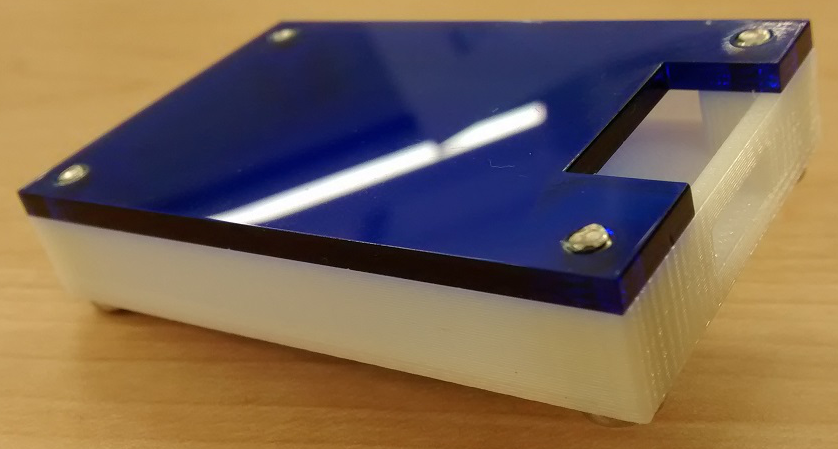
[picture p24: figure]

Figure 7. Example enclosure.

## 3.3 Integration

Demo

/1 Hardware present?

/1 Data sent by hardware

/1 Data retrieved by mobile application

/1 Action initiated by mobile application

/1 Action recieved by hardware

Report

/1 Enterprise wireless connectivity (250)

/1 Database configuration (250 words)

/1 Security considerations (500 words)

/1 Unit testing (900 words)

/1 Production testing (100 words)

### 3.3.1 Enterprise Wireless Connectivity

How did you make a Database accessible by both your Prototype and Mobile Application?

### 3.3.2 Database Configuration

### 3.3.3 Security

### 3.3.4 Testing

Unit testing and Production testing.

# 4.0 Results and Discussions

Is your prototype perfect? What did you learn?

# 5.0 Conclusions

If you were making 1000 of these.

Report

/1 Hardware present?

/1 Checklist truthful

/1 Valid Comments

/1 Results and Discussion (500 words)

/1 Conclusion

# 6.0 References

Gaurav Kumar Maurya, S. K. (2016). Smart Parking Control with LCD Display.

Kahonge, K. E. (2013). MOBILE PHONE –BASED PARKING SYSTEM.

Ms.S.Srikurinji, M. M. (2016, March). SMART PARKING SYSTEM ARCHITECTURE

USING INFRARED DETECTOR. IJAICT.

The journal of design and technology. (2000).

# 7.0 Appendix

## 7.1 Firmware code

Demo

/1 Hardware present?

/3 Code runs concurrently for all sensors/effectors

/1 Project repository contains integrated code

Status

/1 Memo including updates

/1 Financial update

/1 Progress update

/1 Modified Code Files in Appendix

/1 Link to Complete Code in Repository

## 7.2 Application code

Demo

/1 Hardware present?

/1 Memo by student A

/1 Login activity

/1 Data visualization activity

/1 Action control activity

Report

/1 Login activity

/1 Data visualization activity

/1 Action control activity

/1 Modified Code Files in Appendix

/1 Link to Complete Code in Repository

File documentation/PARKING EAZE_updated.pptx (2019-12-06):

## Parking eaze

- Bipolar stepper motor driven by Drv8825 Driver
- Raspberry pi Broadcom
- PRESENTED BY : Navkiran KAUR

## Proposal

- My Hardware project aims to move the barrier in the parking slot for the entrance and exit of the vehicle
- Using the Nema 17 bipolar stepper motor that will be driven by the driver DRV8825 on the raspberry pi Broadcom platform
- The movement of the motor will enhance the direction of the barrier as the motor will rotate in forward and reverse direction.

## Schedule

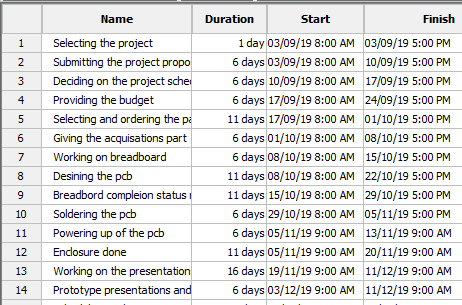
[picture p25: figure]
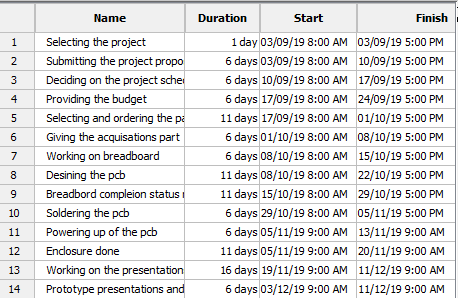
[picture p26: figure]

- Got the delay in my breadboard due to not setting voltage current for driver.
- The pcb was incorrectly designed that leads to the delay
- the enclosure as my case was big which takes time due to taking measurements accurately.

## Budget Total Cost :$173.89

- Raspberry pi : $79.99
- Nema 17 bipolar stepper motor : $12.99
- DRV8825 DRIVER : $14.88
- HDMI TO VGA Cable adaptor : $14.99
- Power supply adaptor: $19.98
- Mouse and Keyboard combo: $25.47
- Safety glasses $5.59
- Parts kit equipments : already had and headers acquired from the prototype lab

## Enclosure

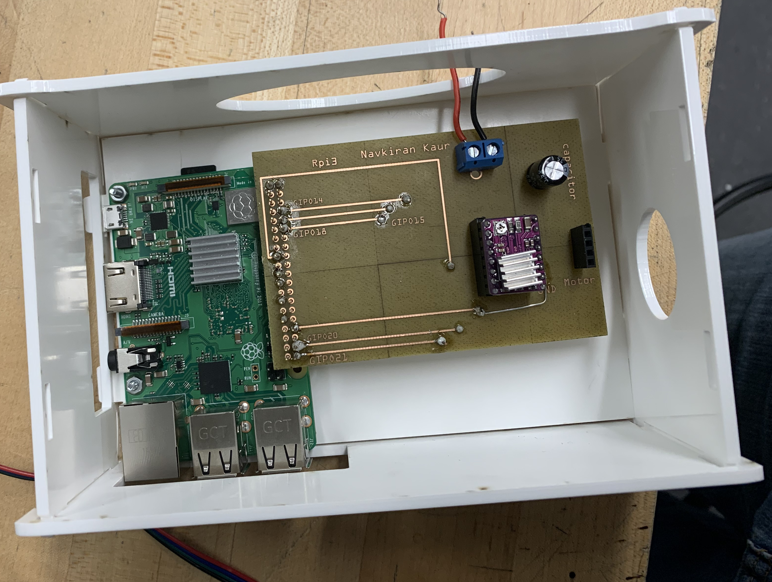
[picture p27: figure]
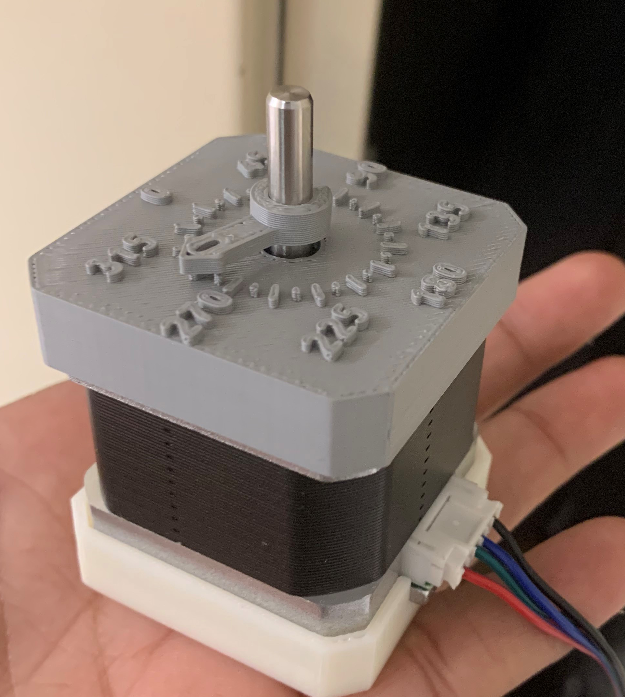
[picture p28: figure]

## Motor movement output

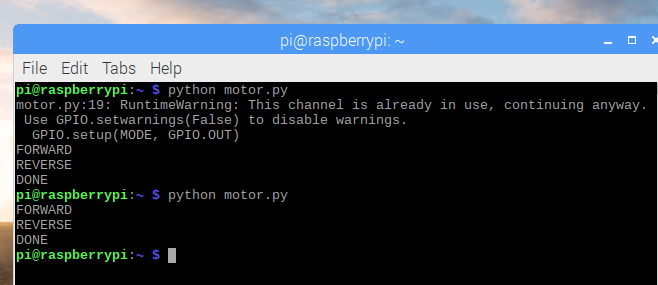
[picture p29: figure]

- The output of the code reading

## Previous courses knoWledge

- Technical c : LEARNT REAGARDING THE RASPBERRY PI
- Unix scripting: commands in the terminal and writing the html code in index.md
- Technical reading and writing skills : prepared the reports
- Digital and interface systems : working with motor and power supplies
- Electric devices and circuits : breadboard connections
- Embedded systems: acquired more knowledge as programming with the raspberry pi

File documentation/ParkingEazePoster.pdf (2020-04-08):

# Project members: Navkiran Kaur,Saina Kapoor and Harleen Kaur Saini Faculty of Applied Science and Technology, Humber College

# ParkingEaze

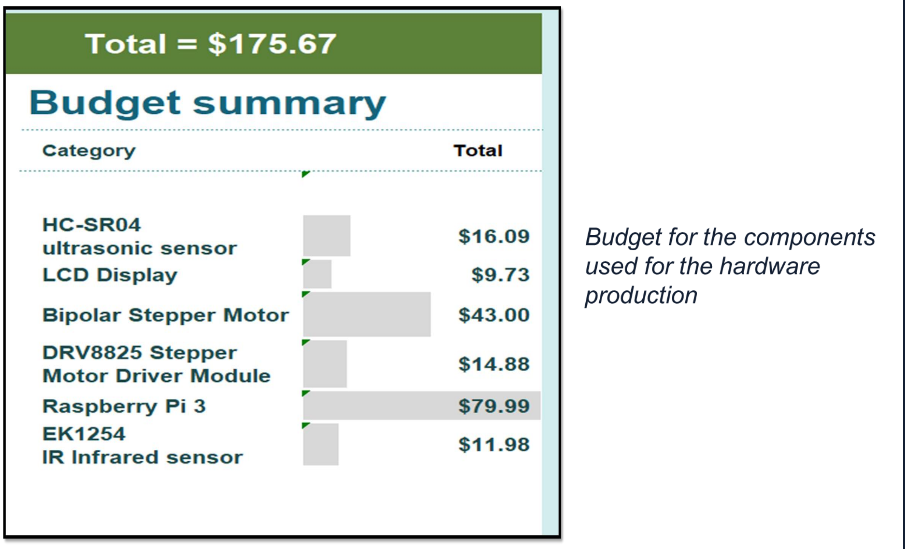
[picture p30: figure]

### ACKNOWLEDGEMENTS

We would like to thank Professor Kristian Medri for their guidance and assistance during the course time, Humber Prototype Lab Staff, Kelly and Vlad for helping in hardware assembly, laser cutting and giving valuable instruction, Prof. Haki Sharifi for their teaching instructions and guiding us to build the android application . We wish to appreciate Humber staff member Colin Buddin and Khaled Ibrahim, as referred by Prof. Kristian Medri, for their support in building 3D printing files in a short period.

## AIM

Parking is a worldwide problem, especially when people are unaware of spaces, costs, and policies that result in a waste of time, crowding and frustration. Our project aims to solve these problems by using such sensors and effectors which in coordination with our mobile application makes it easier for our users to park and pay in a fast and efficient manner. With the help of our technical skills and professor’s guidance, we used the features and key points of different sensors and effectors. The list of Required resources used are

•Infrared sensor

•Ultrasonic sensor

•Bipolar stepper motor

•LCD module

•Raspberry pi

Moreover, the customizable development of the mobile application is being developed to deliver a trustworthy finished product under a low-cost budget.

Bill of materials

Besides parts kit which each of our group members was having other materials budget is given below

## INTRODUCTION

In Today’s world traffic flow, distribution, and accessibility of parking space, have been a major concern to every person in daily routine which makes it an important issue. There is a lot of consummation of time and resources for drivers who spend their precious time driving along the streets in search of parking space and then also going through the long process to pay the parking fees.

To solve this necessity of vehicle parking, we introduce a parking project called ParkingEaze. The ParkingEaze Project enables customers/drivers to online reserve a parking space using the mobile application.

The purpose of this project is to provide the user the convenience to park their vehicle as per their requirement using the app.

## METHOD

The hardware of this project is created by adjoining essential sensors such as HCSR04 ultrasonic sensor, Ek1254 infrared sensor along with effectors like LCD Module and Bipolar stepper motor. Raspberry Pi 3B+ is used as the Broadcom for this project. To connect all the elements, a PCB was created using Fritzing software and Humber Prototype Lab. Functioning of the PCB was tested using the multimeter and connecting it with the VCC and the Ground of it.

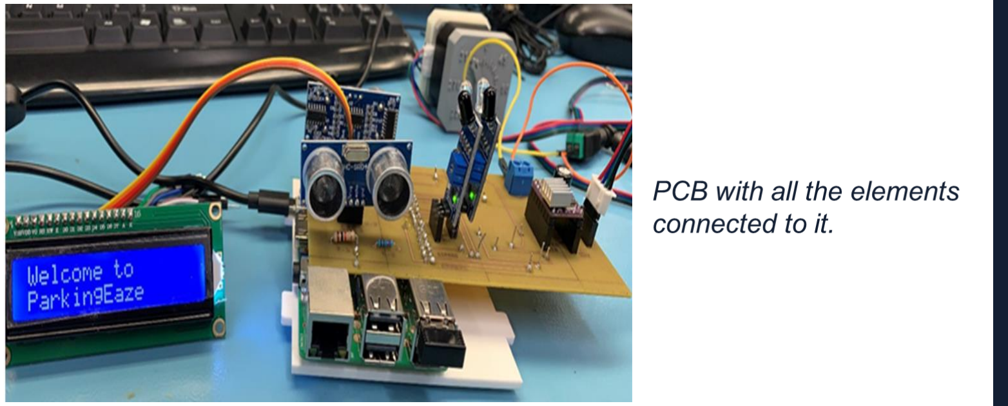
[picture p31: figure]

The firmware of this project was written in python script. It had two major python codes, one for connecting the infrared sensor with the bipolar stepper motor which scan the car before the barrier and give the information to the motor to raise or lower the Barrier. The second code connects the ultrasonic sensor with the LCD which evaluates if there is any car in the parking lot and continuously updates the LCD with the number of parking slots available. Both the codes were able to run by using “&” with it to make it as foreground and background code to keep the track of it.

The firmware code is modified to integrate the hardware with the python code to make the hardware interact with one other. In the previous semester, the hardware components were developed on an individual basis. But now all the sensors and effectors are combined to accomplish an integrated project.

First of all, all the components are tested on the breadboard using the jumper wires after researching how to connect parts along with examining the firmware code too. After knowing that it successfully works on the breadboard, a design for PCB is created. Then, the sensors and effectors are integrated using the PCB which shows the same results as the integration was operative and giving the right results that we have planned to do for the integration.

To sum up, when the vehicle will be to approach the parking space, the barrier will be triggered through the infrared sensor after which the car goes into one of the parking lots. The number on the LCD will be changed immediately for the number of parking lots available with the help of the ultrasonic sensor. It will be changing every time any vehicle enters or exit the parking lot

## RESULTS

The ParkingEaze mobile application provides a reliable user interface and easy to navigate functionality in it. The app. first opens up with a splash screen with a time delay of 3sec to load and then provides the user to:

1. Register as a new user.
2. Login access with the same credentials.
3. Navigate between 2 different parking lots.

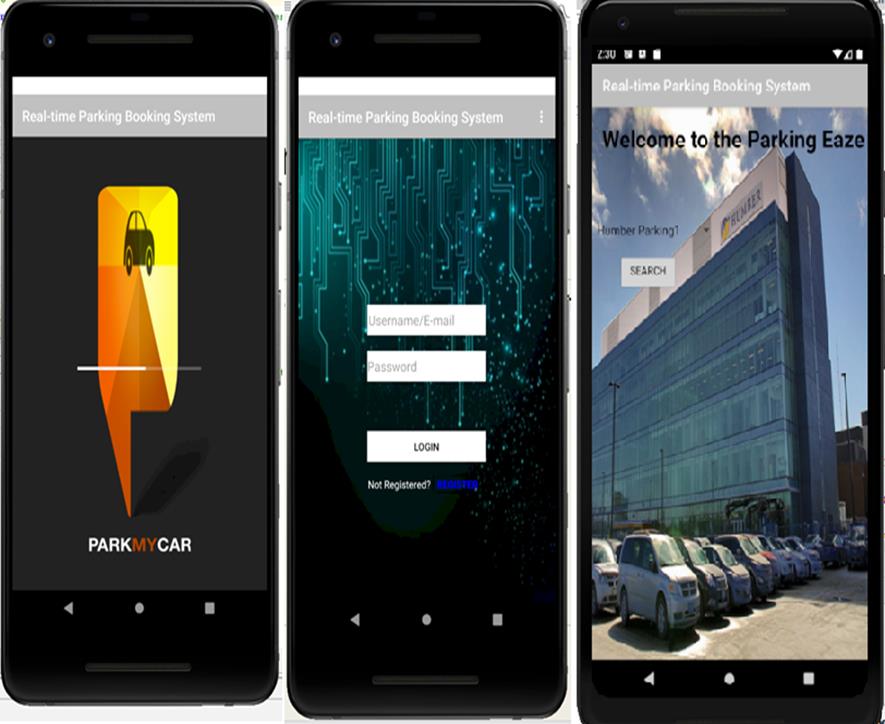
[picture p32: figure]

Once the user is logged in and selected the parking lot, it gives the user access to:
1. Select the date- The date user wants to park the car.
2. Start time – At what time the user wants to park the car in the parking slot.
3.Duration – For how long the user wants to park its car for.

After filling all the necessary details, on clicking the “Show available slots” 6 specific slots will be shown in green color meaning that the slots have not been booked. Once the user selects the slot, it turns the color to red and generated the toast message saying “Slot # booked! ”. For more functionality, this app also provides navigation drawer with information such as “My bookings ” where the user can see all the prior booked slots.

All the information and the selections made by the user are sent to the server-side database connected with the firebase. Here the admin can see the details of the user such as the name of the user, time and date the slot is booked, slot number.

## PRINTING

The case is built using the laser-cut technique and the application used to design the case was the MakerCase. Some necessary changes were made using Corel draw software like adding some holes and slits in the design to give a pathway to the sensors, effector, jumper wires and the motor. The motor covers are made of 3D printing on the top and bottom but it is also covered with acrylic so it gets enclosed completely and properly. Two barriers were also designed one, with the 3D printing technique and the other with the acrylic material. Two acrylic rectangular stands are also included in the design, one is kept at one of the corners of the base just for a better look of the parking lot and the other is designed and placed in the center to hold the LCD which displays the available parking spots.

## CONCLUSIONS

The project for the parking is accomplished to an extent of showcasing it as a finished one. Further improvements can be done in the android application to make it more effective and user-friendly. Moreover, new features can be included in the design and functionality such as providing more options for the user. The experience of making the android application and hardware production provides the necessary skills which make us being capable of moving to advance steps for the project development. We are moving forward to fix the errors and troubleshooting the software application along with working on the database. Although hardware components are integrated and work accordingly yet further changes and modifications can be considered to grow the parking space for additional plans in the future. Overall, the project has allowed us to solve a real-world problem through this course as we learn vital technical skills and knowledge using both hardware and software.

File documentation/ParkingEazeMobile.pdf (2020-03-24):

## Mar 24/25 Mobile application update

## ParkingEaze Mobile

Grading for this milestone:

/1 Completed: Survey regarding substantial completion of this term

/1 Participated: Online session

/2 Login activity

/2 Data visualization activity

/2 Action control activity

/1 Modified Code Files in Appendix

/1 Link to Complete Code in Repository

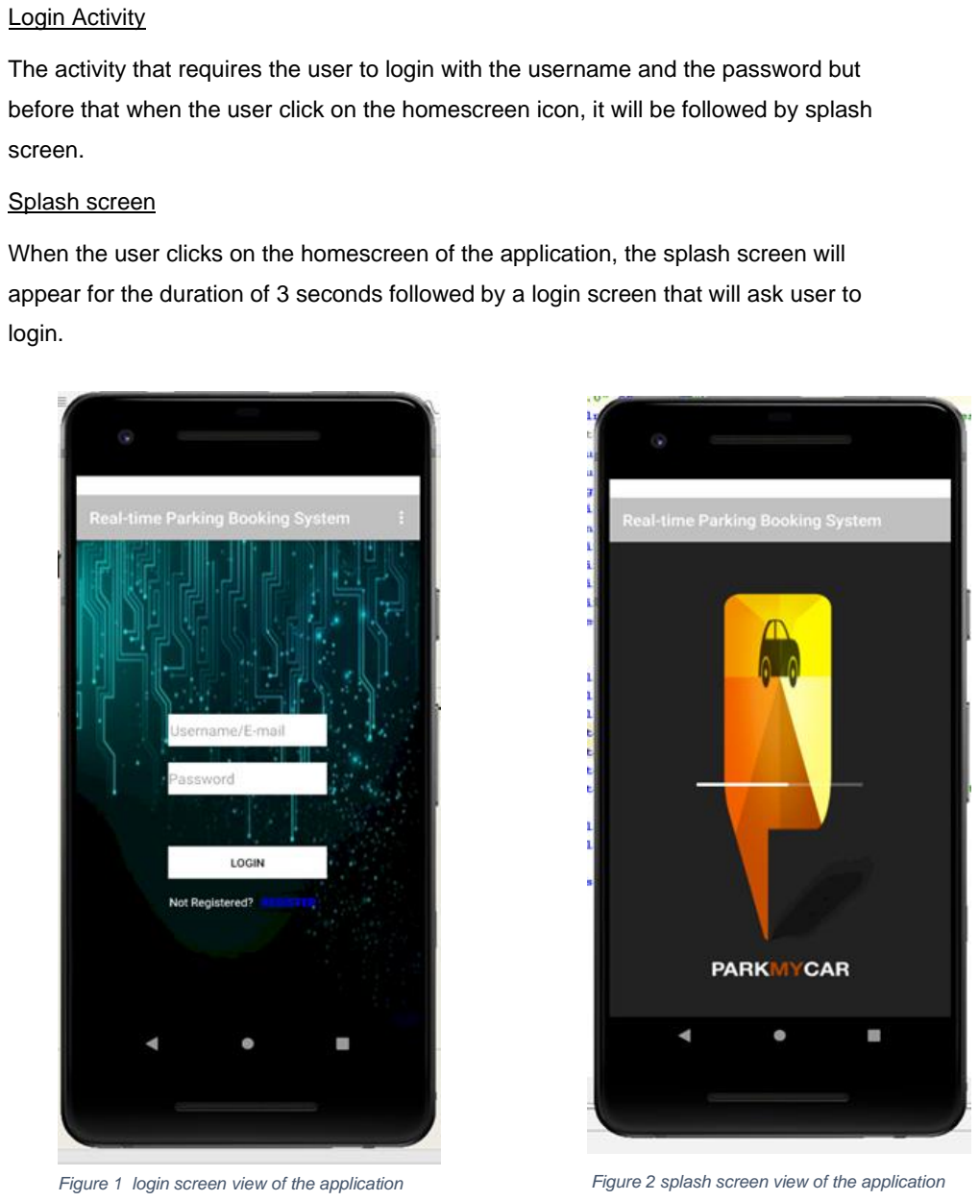
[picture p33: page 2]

Login Activity

The activity that requires the user to login with the username and the password but

before that when the user click on the homescreen icon, it will be followed by splash

screen.

Splash screen

When the user clicks on the homescreen of the application, the splash screen will

appear for the duration of 3 seconds followed by a login screen that will ask user to

login.

Figure 1 login screen view of the application | Figure 2 splash screen view of the application

Then comes the login screen where the user will have ability to enter the username and

the password in order to login the application. It also has the option to register which will

let the user for registration if the user is not registered yet.

Action Control Activity

After the user is logged in the mobile application, the location for the parking the vehicle

are to be chosen from three options which are Humber Parking1, Humber Parking2 and

Humber Parking3(Figure 3). The dialog box is displayed which shows these choices to

user. When the user clicks on one of the options then a new screen appears which asks

the user to choose an empty parking spot(Figure4). The slot turns green to red

(Figure5)after the user booked it and therefore the spot to park the vehicle has been

booked by the customer through the android application. Also, when the user opens the

mobile application, it displays a runtime permission asking the user to provide the

location access to the android application.

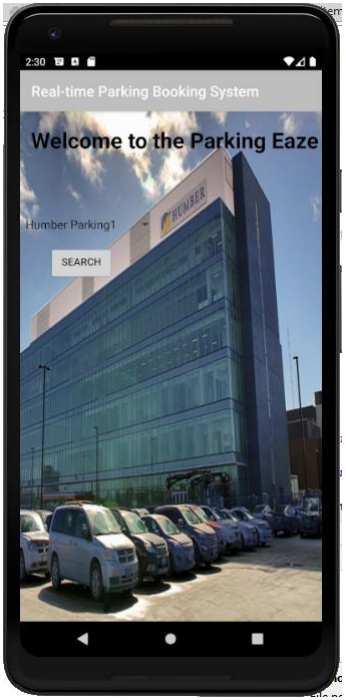
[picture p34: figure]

Figure 3 ;user asked to choose the parking location

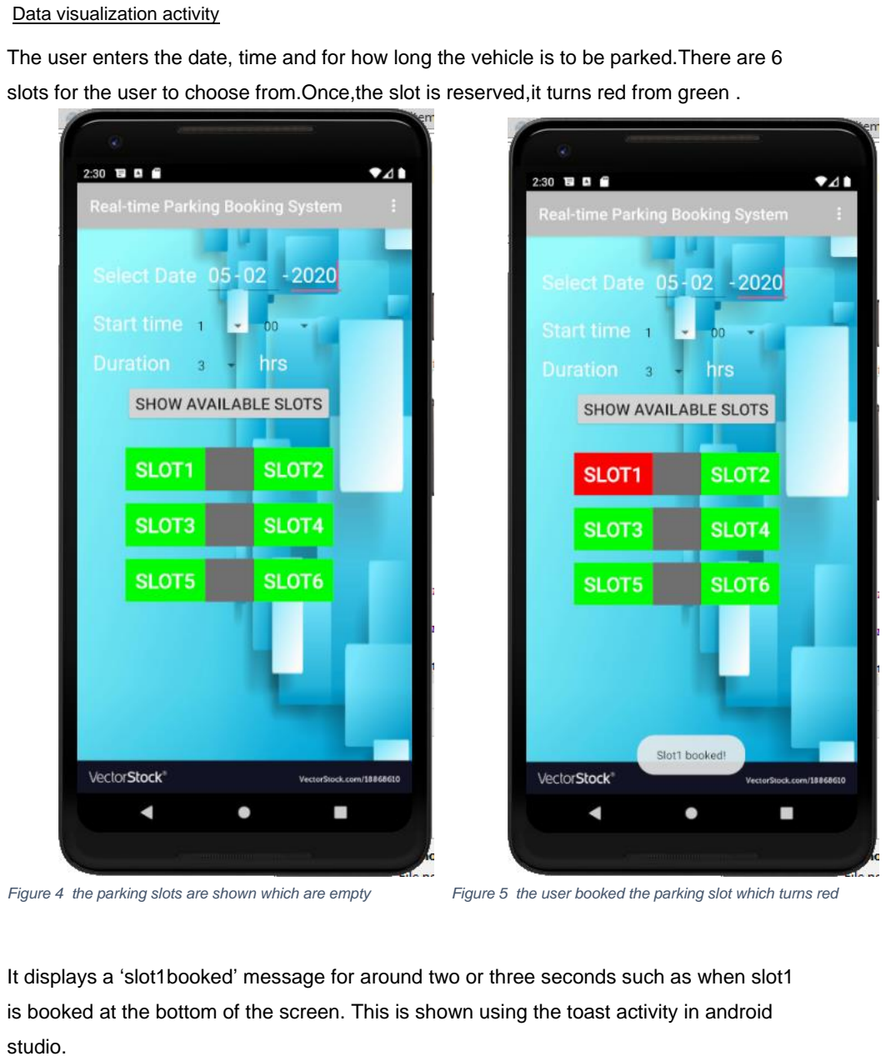
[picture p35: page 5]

Data visualization activity

The user enters the date, time and for how long the vehicle is to be parked.There are 6

slots for the user to choose from.Once,the slot is reserved,it turns red from green .

It displays a ‘slot1booked’ message for around two or three seconds such as when slot1

is booked at the bottom of the screen. This is shown using the toast activity in android

studio.

Figure 4 the parking slots are shown which are empty | Figure 5 the user booked the parking slot which turns red


Figure 1 the navigation drawer layout has been implemented

The above figure shows the navigation drawer layout feature used to display options for

the user to choose from.

Link to complete code files in repository.

https://github.com/NavkiranKaur/ParkingEaze/tree/master/code%20files


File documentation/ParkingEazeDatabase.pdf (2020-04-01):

### ParkingEaze

### Database connections functionality update

This document provides the information regarding the functionality of the database in the android mobile application. The demonstration has been held during the online class session for the database connection. The database is stored and saved in the firebase for the android application.

Grading for this milestone:

/1 Participated: Online session

/4 Online demo

/1 Addresses connection to enterprise wireless (v.s. home/open Wi-Fi/hotspot)

/1 Database configuration mentioned

/1 Security considered

/2 Unit and production testing considerations

Database configuration

Firebase Implementation for our database

A firebase project is created using a username and password then firebase is added with the android application project in the android studio. The data is stored in the JSON format along with providing an offline facility of data storage by enabling the disk persistence. After creating firebase project, the android application can be registered to it. Firebase also supports to focus on performance and implementation issues by repairing bugs precisely from its backend solution.However,our group have experienced many problems in order to connect to firebase.Eventually,we are able to display the users in the firebase , who are logged in the application.


Figure 1 The information stored in the firebase is displayed

Addresses connection to enterprise wireless

The connection is established using the wireless network which is WIFI. The application uses the internet using the runtime permission feature in the android studio which is provided in the AndroidManifest.xml file. The connection can be established in order to access the internet.

<uses-permission android: name="android. permission. INTERNET"/>


Figure 2 The AndroidManifest.xml file in android studio

Consideration of security:

The security of the application used by the user is enhanced as shown in figure3 and Figure4 below. When the user opens the application, a dialog box appears which prompts a message whether the user wants to provide the location access to the application that follows user’s privacy. It also assures and reminds them if they want to exit without the submission of any changes when the user clicks exit option. Hence,instead of instantly closing the app, a dialog box is prompted.


Figure 4 Asking the user if the user wants to leave without submitting their changes.


Figure 3 Asking permission to use the current location before seeing the nearby parking lots.

Unit Testing

In the figure below, the testing is done for software validation code of some cases. The test cases are implemented and tested step by step which are eventually passed. Performing unit tests is intended to be uncomplicated, generally the tests are written in the structure of functions that will decide whether a returned value equals the value you were anticipating when you entered the function in the software code.


Figure 5 The test cases for the validation are tested and all of them are passed

Production Testing

The application connected to the firebase and once the application is complete and if it is eligible to be launched on the google play store, then the users can download it from there based on their requirement. The hardware consists of the sensors and effectors which comply differently according to the production testing.

- UtilsTest.java containstesting functions from the code and the code can be found through this link
- https://github.com/NavkiranKaur/ParkingEaze/blob/master/code%20files/UtilsTest.java (https://github.com/NavkiranKaur/ParkingEaze/blob/master/code%20files/UtilsTest.java)
- The main activity java file that contains firebase connection code can be found using this link below
- https://github.com/NavkiranKaur/ParkingEaze/blob/master/code%20files/MainActivity.java (https://github.com/NavkiranKaur/ParkingEaze/blob/master/code%20files/MainActivity.java)

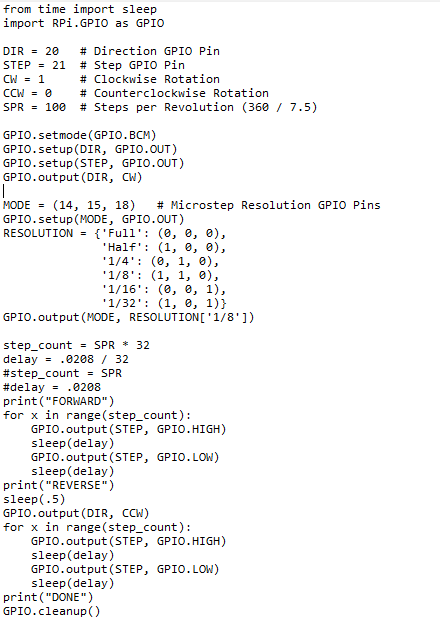
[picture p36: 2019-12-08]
images/codeblog.PNG

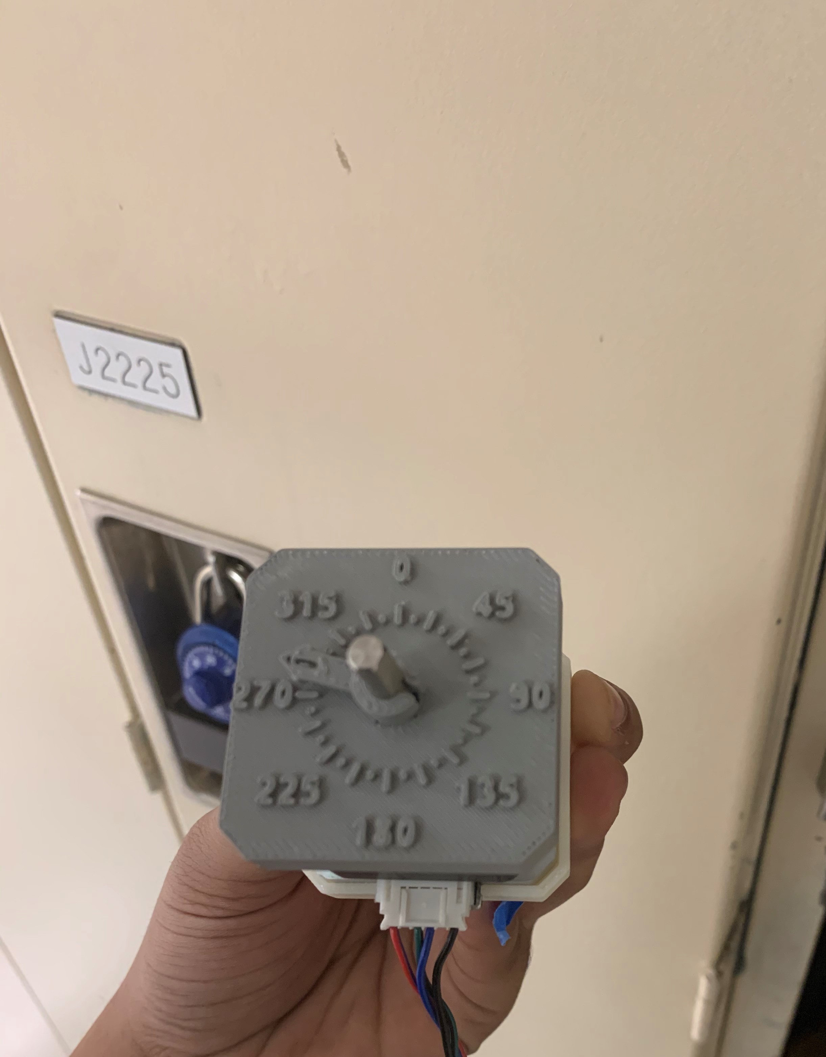
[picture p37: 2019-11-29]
images/motor1.jpg

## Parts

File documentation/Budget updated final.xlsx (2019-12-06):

Quantity | Name of the product | Product Description | PartSupplier | Part Number | Cost | SHIPPING | Tax | Subtotal
1 | Raspberry Pi 3 Model B+ Plus Starter Kit with 5v3a Charger | Raspberry Pi 3 (RPi3) Model B+ 64-bit Quad-Core 1.4 GHz 1 GB RAM 16GB (Class 10)Micro SD Card Preloaded with NOOB v2.8+ UL Listed 3 Amp USB Power Supply with Micro USB Cable and Noise Filter - designed for the Raspberry Dual Band 2.4GHz and 5GHz IEEE 802.11.b/g/n/ac Wireless LAN, Enhanced Ethernet Performance MicroSD USB 2.0 Adapter and 1m HDMI Cable | AMAZON | B07HF7BCFC | CDN $79.99 | free-shipping | $0.00 | CDN $ 79.99
1 | Usongshine 38mm 4 Lead Nema17 Stepper Motor Nema 17 Motor 42BYGH 38MM 1.5A (17HS4401) Motor for CNC XYZ 3D | 17HS4401 1PCS 38mm 4 Lead Nema17 1pcs 38mm Stepper Motor/1pcs 1m XH2.54 4pins cables and connector (Size: 42mm X 42mm X 38mm/1.65''x1.65''x1.49'' ,NEMA 17 bipolar 4-wires | Amazon | Usongshine motor1 | CDN$ 12.99 | free shipping | $0.00 | CDN$ 12.99
1 | GutReise 100-240V to 3V,4.5V,5V,6V,7.5V,9V,12V 30W 2A&2000mA Multifunction Adjustable AC/DC Charger | Adapter Switching Power Supply +5Vnput:100-240V 0.25A 50/60Hz, DC Output:3V/4.5V/5V/6V/7.5V/9V/12V.USB port:5V 2.1A. | Amazon | 3-12v adapter | CDN$ 19.98 | free-shipping | $0.00 | CDN$ 19.98
1 | 5pcs DRV8825 Stepper Motor Driver Module for 3D Printer RepRap 4 RAMPS1.4 StepStick | DRV8825 Stepper Motor Driver Module 45 V maximum supply voltage 4-layer, 2 oz copper PCB for improved heat dissipation Can interface directly with 3.3 V and 5 V systems Simple step and direction control interface | Amazon | No.=606321399948 | CDN$ 14.88 | free shipping | $0.00 | CDN$ 14.88
1 | Hdmi to vga adaptor | VicTsing HDMI to VGA Adapter, Gold-Plated 1080P HDMI Female to VGA Male Adapter with a 3.5mm Audio Cable, | Amazon | CAAA1-VTVTPC198AB | CDN$14.99 | free-shipping | $0.00 | CDN$14.99
1 | safety glasses | MCR Safety Crews SS110 Stratos Safety Glasses Polycarbonate Clear Lens, Nylon Black Frame, 1 Pair | Amazon | SS110 | CDN$4.95 | FREE-SHIPPING | $0.64 | CDN$5.59
1 | Logitecg mouse and keyboard combo | Logitech MK235 Wireless Keyboard and Mouse Grey English it isCombo is a simple plug-and play keyboard and mouse with a reliable wireless connection up to 10m/33ft away, sharing one tiny USB receiver. | walmart | 920-007897 | CDN$24.98 | BOUGHT IN PERON DISCOUNT:2.498 | $2.99 | CDN$25.47
Total cost of all equipments: |  |  |  |  |  |  |  | CDN$173.89
tools and parts already available :
1 | Electrical Parts Kit | Jumper wires, Resistors, Bread board, led lights, alligator and banana clips, wires, capacitors etc. | Humber Bookstore | EL-CK-003 | $120.00 | bought in person | $15.60 | CDN$ 135.60
5 | headers and sockets | double row male to female headers 40 pin, single row 8 pins ,a 4 pin and a 4 pin male to male | prototyoe lab |  | $0.00 | in person | CDN$0.00 | CDN $0.00
4 | MOTOR 3D PRINT PARTS | BOTTOM,TOP ,ARROWS , | prototype lab,NB building profs,humber College |  | $0.00 | IN PERSON | CDN$0.00 | CDN$0.00
1 | CASE | white case for enclosure | prototype lab |  | $0.00 | in person | CDN$0.00 | CDN$0.00

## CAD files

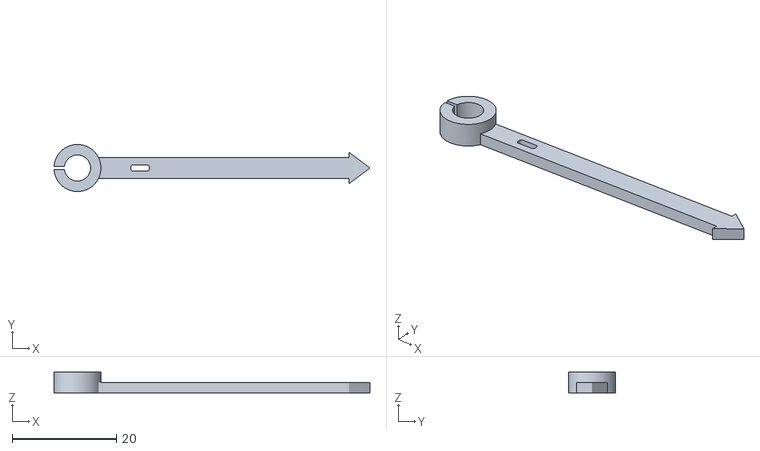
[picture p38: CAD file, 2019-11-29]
mechanical/Nema 17 motor 3D printing files/motor_cover_arrow2 (1).stl
60.5 x 9.00 x 4.00

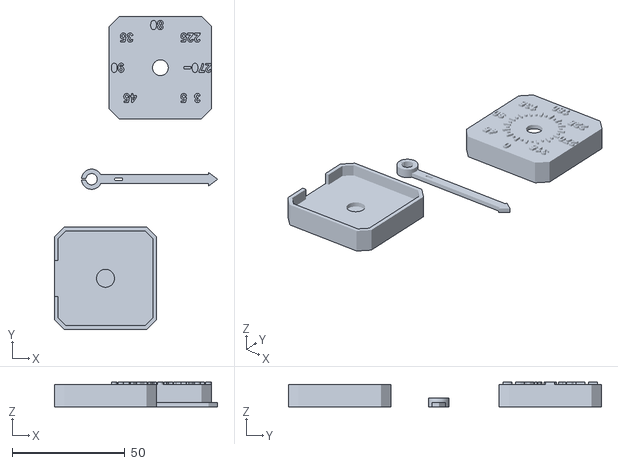
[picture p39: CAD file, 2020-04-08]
mechanical/ParkingEazeDesign3D.stl
72.6 x 139.1 x 11.0

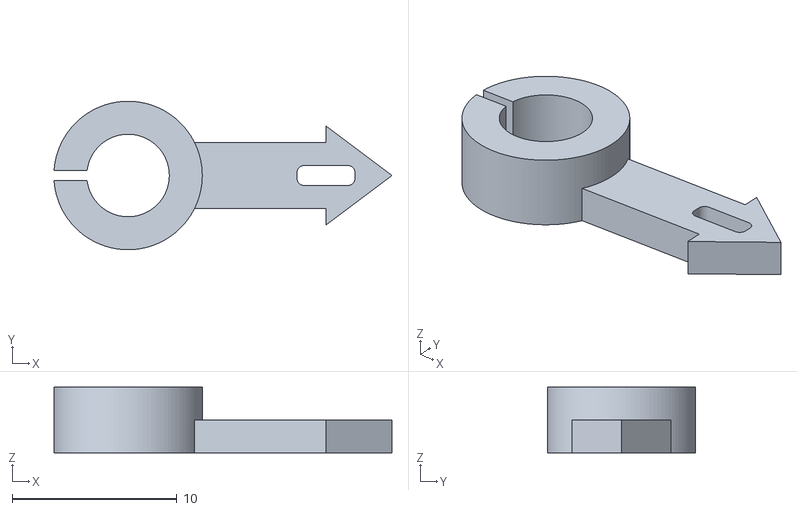
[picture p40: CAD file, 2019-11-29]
mechanical/Nema 17 motor 3D printing files/motor_cover_arrow1.stl
20.5 x 9.00 x 4.00

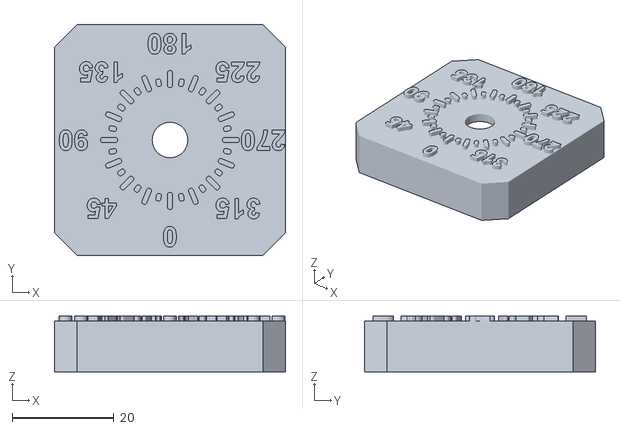
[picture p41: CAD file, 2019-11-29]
mechanical/Nema 17 motor 3D printing files/motor_cover_top.stl
45.5 x 45.5 x 11.0

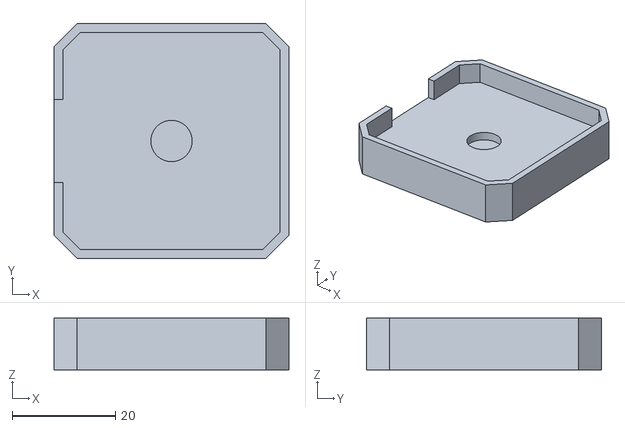
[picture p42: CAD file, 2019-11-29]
mechanical/Nema 17 motor 3D printing files/motor_cover_bottom.stl
45.5 x 45.5 x 10.0

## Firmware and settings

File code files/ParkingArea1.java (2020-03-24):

//parkingEazeTeam
package eaze.parking;

import android.graphics.Color;
import android.os.Bundle;

import androidx.fragment.app.Fragment;

import android.text.TextUtils;
import android.view.LayoutInflater;
import android.view.View;
import android.view.ViewGroup;
import android.widget.AdapterView;
import android.widget.ArrayAdapter;
import android.widget.Button;
import android.widget.EditText;
import android.widget.Spinner;
import android.widget.TextView;
import android.widget.Toast;


import com.google.firebase.auth.FirebaseAuth;
import com.google.firebase.database.DataSnapshot;
import com.google.firebase.database.DatabaseError;
import com.google.firebase.database.DatabaseReference;
import com.google.firebase.database.FirebaseDatabase;
import com.google.firebase.database.Query;
import com.google.firebase.database.ValueEventListener;

import java.text.SimpleDateFormat;
import java.util.Calendar;
import java.util.Date;

import eaze.parking.Booking;
import eaze.parking.R;

public class ParkingArea1 extends Fragment {
    private String location = "ParkingArea1";
    private TextView Heading;
    private EditText dd;
    private EditText mm;
    private EditText yyyy;
    private Spinner startTime;
    private Spinner startmins;
    private Spinner duration;
    private String start;
    private String durationhrs;
    private String minstart;
    private Button slot1;
    private Button slot2;
    private Button slot3;
    private SimpleDateFormat mdformat;
    private Button slot4;
    private String enterstartdate;
    private Button slot5;
    private Date enteredstart=null;
    private Date enteredend=null;
    private Button slot6;
    private Button showslots;
    private boolean slot1flag = false;
    private boolean slot2flag = false;
    private boolean slot3flag = false;
    private boolean slot4flag = false;
    private boolean slot5flag = false;
    private boolean slot6flag = false;
    private int d;
    private int month;
    private int year;
    private int currenthours;
    private int currentmins;
    private FirebaseDatabase firebaseDatabase;
    private DatabaseReference bookingReference;
    Calendar calendar;

    @Override
    public View onCreateView(LayoutInflater inflater, ViewGroup container,
                             Bundle savedInstanceState) {
        // Inflate the layout for this fragment
        if (container != null) {
            container.removeAllViews();
        }
        View view = inflater.inflate(R.layout.fragment_parkingarea, container, false);
       // if (getArguments() != null) {
           // location = getArguments().getString("location");
      //  }

              calendar = Calendar.getInstance();

      //  firebaseDatabase = FirebaseDatabase.getInstance();
      //  bookingReference = firebaseDatabase.getReference().child("Bookings");

        slot1 = (Button) view.findViewById(R.id.ParkingArea1_slot1);
        slot2 = (Button) view.findViewById(R.id.ParkingArea1_slot2);
        slot3 = (Button) view.findViewById(R.id.ParkingArea1_slot3);
        slot4 = (Button) view.findViewById(R.id.ParkingArea1_slot4);
        slot5 = (Button) view.findViewById(R.id.ParkingArea1_slot5);
        slot6 = (Button) view.findViewById(R.id.ParkingArea1_slot6);
        showslots = (Button) view.findViewById(R.id.show_slots);
        dd = (EditText) view.findViewById(R.id.ParkingArea1_start_dd);
        mm = (EditText) view.findViewById(R.id.ParkingArea1_start_mm);
        yyyy = (EditText) view.findViewById(R.id.ParkingArea1_start_yyyy);
        showslots.setOnClickListener(new View.OnClickListener() {
            @Override
            public void onClick(View view) {
                if (TextUtils.isEmpty(dd.getText().toString())) {
                    dd.setError("Enter date");
                    return;
                }
                if (TextUtils.isEmpty(mm.getText().toString())) {
                    mm.setError("Enter month");
                    return;
                }
                if (TextUtils.isEmpty(yyyy.getText().toString())) {
                    yyyy.setError("Enter year");
                    return;
                } else {
                    mdformat = new SimpleDateFormat("yyyy/MM/dd HH:mm");
                    Date currentdate=null;
                    try {
                         currentdate = mdformat.parse(mdformat.format(calendar.getTime()));
                    }
                    catch (Exception c){
                        c.printStackTrace();
                    }
                     enterstartdate=yyyy.getText().toString()+"/"+mm.getText().toString()+"/"+dd.getText().toString()
                            +" "+start+":"+minstart;


                    try {
                        enteredstart = mdformat.parse(enterstartdate);
                        Calendar cal = Calendar.getInstance(); // creates calendar
                        cal.setTime(enteredstart); // sets calendar time/date
                        cal.set(Calendar.HOUR_OF_DAY, cal.get(Calendar.HOUR_OF_DAY)+Integer.parseInt(durationhrs));
                        System.out.println("checkff"+ mdformat.format(cal.getTime()));
                        enteredend=cal.getTime();
                    }
                    catch (Exception c){
                        c.printStackTrace();
                    }
                    System.out.println("checkff value="+currentdate.compareTo(enteredstart));
                    if (currentdate.compareTo(enteredstart)==1) {
                        Toast.makeText(getActivity(), "Entered date is less than current date!", Toast.LENGTH_SHORT).show();
                        dd.setText("");
                        mm.setText("");
                        yyyy.setText("");
                        return;
                    }
                }
                slot1.setVisibility(View.VISIBLE);
                slot2.setVisibility(View.VISIBLE);
                slot3.setVisibility(View.VISIBLE);
                slot4.setVisibility(View.VISIBLE);
                slot5.setVisibility(View.VISIBLE);
                slot6.setVisibility(View.VISIBLE);
                slot6.setBackgroundColor(Color.GREEN);
                slot2.setBackgroundColor(Color.GREEN);
                slot3.setBackgroundColor(Color.GREEN);
                slot4.setBackgroundColor(Color.GREEN);
                slot5.setBackgroundColor(Color.GREEN);
                slot1.setBackgroundColor(Color.GREEN);
                slot1flag = false;
                slot2flag = false;
                slot3flag = false;
                slot4flag = false;
                slot5flag = false;
                slot6flag = false;
               // checkBookedSlots();
            }
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

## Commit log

2020-03-17 The design file for enclosure
2020-03-24 layout .xml files
    [app_bar_login_screen_navigation.xml]
2020-04-08 Laser cut design file
2020-04-08 Stepper motor 3D design
    [ParkingEazeDesign3D.stl]
